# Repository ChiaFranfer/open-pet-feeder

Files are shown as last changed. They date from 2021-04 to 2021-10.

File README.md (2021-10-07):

# Open Pet Feeder

Trabajo final de estudios para finalizar mi titulación 'Ingeniería en Sistemas de Telecomunicación', en la Universidad Politécnica de Cartagena. 
* Nombre del trabajo: `Diseño y automatización de un sistema de alimentación OpenSource para animales a través de la tecnología LoRa`
* Promoción: `2020-2021`

## Objetivos
- Diseñar un sistema de alimentación para animales con tecnologías Open Source.
- Realizar simulaciones para el enlace radio entre el refugio de animales y el emplazamiento de nuestro gateway.
- Construir el prototipo y probarlo en entorno controlado y, posteriormente, en entorno definitivo (refugio).

## Logros conseguidos

- El dispositivo del refugio es apto para trabajar en zonas sin conexión a internet y sin red eléctrica.
- Control remoto de un dispositivo apto para alimentar y abrevar animales.
- Enlace radio LoRa directo (sin repetidores) a varios kilómetros entre gateway y dispositivo.
- Página web de control y envío de comandos al dispositivo.
- Kit gateway + dispositivo, por debajo de 100 euros.

## Tecnologías utilizadas
* Arduino Nano
* Trasnceptor LoRa E32-868T30D
* Raspberry Pi 3
* PCB custom diseñada con EasyEDA

## Imagenes de los dispositivos
### Dispositivo de alimentación y abrevadero


### PCB del dispositivo


## Esquemático del proyecto
### Comedero
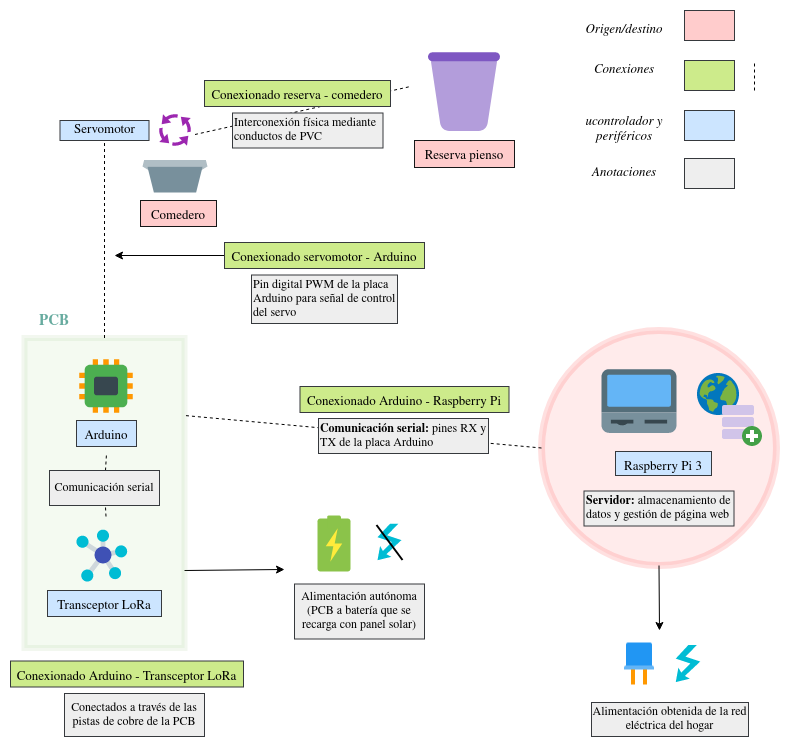
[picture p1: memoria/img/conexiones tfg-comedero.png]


### Bebedero
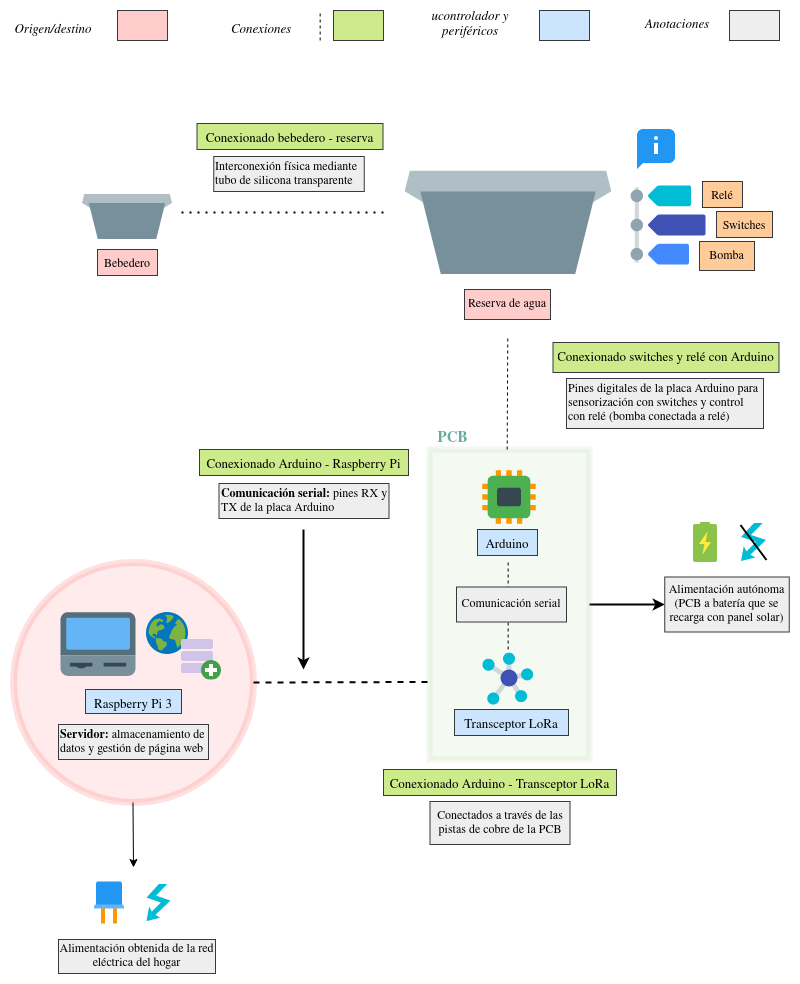
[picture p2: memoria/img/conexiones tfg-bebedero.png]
Diagrama bebedero


### Web


## Documentación
Toda la documentación del proyecto la podemos encontrar en la carpeta: `memoria`. El código utilizado en los diferentes dispositvos se encuentra en la carpeta `software`, y los esquemáticos de la PCB están en la carpeta: `hardware`.

El documento definitivo que se publicará por la universidad está en: `memoria/memoria_definitivo.pdf`

## Autor

- [@ChiaFranfer](https://www.github.com/chiafranfer)

## Licencia
Todo el código del repositorio está bajo la licencia MIT. Los documentos LaTeX y sus PDFs correspondientes pertenecen al autor del proyecto. El trabajo definitivo será publicado por la institución: Universidad Politécnica de Cartagena.

[MIT](https://choosealicense.com/licenses/mit/)

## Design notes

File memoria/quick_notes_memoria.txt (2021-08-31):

## Anotaciones

- Se recomienda ver el tipo de licencia que tiene cada proyecto, ya que aunque sean Open Source, 
presentan por norma general licencias que, como mínimo, exigen que se mencione al creador debidamente.

## Refs a anexos
\hyperref[anexo I: ficha tecnica]{Anexo I}
\hyperref[anexo II: codigo]{Anexo II}
\hyperref[anexo III: presupuesto]{Anexo III}

## Comillas

`` hdajhdahkd ''

## Hackeo de imagenes: 5 imagenes
	\begin{figure}
		\begin{center}
			\begin{tabular}{cc}
				\includegraphics[width=50mm]{img/Fotos comedero/pieza1_comedero.jpg} &   \includegraphics[width=50mm]{img/Fotos comedero/pieza2_comedero.jpg} \\
				(a) Pieza 1 PVC & (b) Pieza 2 PVC \\[6pt]
				\includegraphics[width=50mm]{img/Fotos comedero/pieza3_comedero.jpg} &   \includegraphics[width=50mm]{img/Fotos comedero/pieza4_comedero.jpg} \\
				(c) Pieza 3 PVC & (d) Pieza 4 PVC \\[6pt]
				\multicolumn{2}{c}{\includegraphics[width=50mm]{img/Fotos comedero/pieza5_comedero.jpg} }\\
				\multicolumn{2}{c}{(e) Pieza 5 PVC}
			\end{tabular}
			\caption{Zoom de las piezas que conforman el sistema de conexionado entre reserva y comedero.}
			\label{Prototipo: piezas PVC reserva-comedero}
		\end{center}
	\end{figure}

## Hackeo de imagenes: 2 imagenes

	\begin{figure}
		\begin{center}
			\begin{tabular}{cc}
				\includegraphics[width=50mm]{img/Fotos comedero/pieza1_comedero.jpg} &   \includegraphics[width=50mm]{img/Fotos comedero/pieza2_comedero.jpg} \\
				(a) Pieza 1 PVC & (b) Pieza 2 PVC \\[6pt]
			\end{tabular}
			\caption{Zoom de las piezas que conforman el sistema de conexionado entre reserva y comedero.}
			\label{Prototipo: piezas PVC reserva-comedero}
		\end{center}
	\end{figure}

## Revisar

	Integridad mediante prototipo exterior. Cambiar un poco maybe lo que es el título.

	\item \textbf{Integridad mediante prototipo exterior}. Se entiende por \textit{Integridad mediante prototipo exterior} todos aquellos 
	elementos que usemos para dar forma al proyecto, evitando el uso de elementos demasiado temporales como pueden ser una protoboard o en 
	general, componentes no definitivos (estos sólo se usarán en pruebas, no en producción). Con esta  idea, se buscarán elementos que 
	permitan constituir un primer prototipo usable, sin invertir excesivo dinero, que elimine componentes temporales no funcionales para usar 
	en la ubicación real; es por ello, que se cuenta con la inversión en reservas, conexionado de reserva a comedero/bebedero, diseño de una PCB, etc.

	Apartado 4.2.1.2. Bebedero
	Apartado 4.2.1.1. Comedero

	Explicación de las pruebas de campo -- HECHO
	Explicación de las pruebas de interior

	Explicación del por qué de elegir los E32 (características técnicas)

	Bloque "Software Arduino" -- HECHO

	Fotos Arduino nano

	Foto conglomerado alimentación soldado -- HECHO

## Bib Arduino memory

bib: arduino memory foundations
bib: seeedstudio arduino memory
bib: electronicsHub arduino memory

## Bib bootloader

bib: Arduino cc  bootloader
bib: baldEngineer arduino bootloader

## Bib para leer SPI, uart

https://www.arduino.cc/en/reference/SPI
https://www.circuitbasics.com/basics-of-the-spi-communication-protocol
https://www.circuitbasics.com/basics-uart-communication/

## Insertar una imagen

	\begin{figure}[h]
		\begin{center}
			\includegraphics[width=0.6\textwidth]{img/LPWAN_comp.png}
			\caption{Comparativa entre LPWAN, en términos de alcance y ancho de banda, con respecto a otras comunicaciones inalámbricas [\ref{bib: iotforall lpwan options}].}
			\label{LPWANs vs otros}
		\end{center}
	\end{figure}

## Copiar código a memoria

\begin{lstlisting}[language=C]

\end{lstlisting}

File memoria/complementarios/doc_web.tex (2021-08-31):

\documentclass[12pt]{article}
\usepackage[spanish, english, es-tabla]{babel}
\usepackage[utf8]{inputenc}
\usepackage{amsmath,amssymb}
\usepackage{graphicx}
\usepackage{gensymb}
\usepackage{outlines}
\usepackage[export]{adjustbox}
\usepackage{adjustbox}
\usepackage{multicol}
\usepackage{lipsum}
\parskip 1ex

\usepackage{eurosym}

% add code
\usepackage{listings}

\usepackage{array}

% text font 

\usepackage{courier}

%\usepackage{fontspec}

\usepackage[dvipsnames]{xcolor}

\usepackage{hyperref}
\usepackage{subcaption}
\usepackage[left = 2cm, right = 2cm, bottom = 2cm, top = 3cm]{geometry}

\hypersetup{
	colorlinks=true,
	linkcolor=black,
	%filecolor=magenta,      
	urlcolor=cyan,
}

\hypersetup{
	pdftitle= {Diseño y automatización de un sistema de alimentación OpenSource para animales a través de la tecnología LoRa},
	pdfauthor = {Lucía Francoso Fernández},
	pdfsubject = {Electrónica y comunicaciones móviles},
	pdfkeywords = {Arduino, LoRa, automatización, LoRaWAN, punto a punto, OpenSource}
}

% define color for C code (Anexos)

\definecolor{codegreen}{rgb}{0,0.6,0}
\definecolor{codegray}{rgb}{0.5,0.5,0.5}
\definecolor{codepurple}{rgb}{0.58,0,0.82}
\definecolor{backcolour}{rgb}{0.95,0.95,0.92}

\lstdefinestyle{mystyle}{
	backgroundcolor=\color{backcolour},   
	commentstyle=\color{codegreen},
	keywordstyle=\color{magenta},
	numberstyle=\tiny\color{codegray},
	stringstyle=\color{codepurple},
	basicstyle=\ttfamily\footnotesize,
	breakatwhitespace=false,         
	breaklines=true,                 
	captionpos=b,                    
	keepspaces=true,                 
	numbers=left,                    
	numbersep=5pt,                  
	showspaces=false,                
	showstringspaces=false,
	showtabs=false,                  
	tabsize=2
}

\lstset{style=mystyle}

% https://tex.stackexchange.com/questions/60209/how-to-add-an-extra-level-of-sections-with-headings-below-subsubsection
\newcommand{\subsubsubsection}[1]{\paragraph{#1}\mbox{}\\}
\setcounter{secnumdepth}{4}
\setcounter{tocdepth}{4}

\begin{document}
	\selectlanguage{spanish}
	
	%\thispagestyle{empty}

	%\pagebreak
	
	\thispagestyle{empty}
	
	\newgeometry{left=0.01cm,bottom=0.01cm, top=0.01cm}
	
	%width=0.3\textwidth,
	
	%\begin{figure}[h!]
	%	\includegraphics[height=\textheight,left]{img/banda_etsit_90.png}
	
	%	\end{figure}
	
	\begin{minipage}{0.2\textwidth}
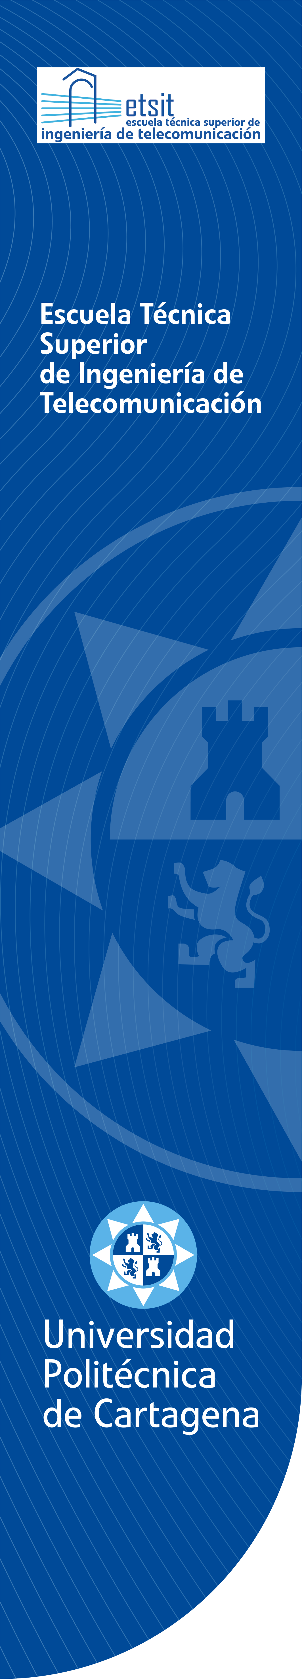
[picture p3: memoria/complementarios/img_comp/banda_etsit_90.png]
		
	\end{minipage}
	\centerline{\begin{minipage}[t][7cm][b]{0.5\textwidth}
			%	\textbf{UNIVERSIDAD POLITÉCNICA DE} \\
			
			%	\textbf{CARTAGENA}\\
			
			\vspace{2cm}
			
			\title{\textbf{Automatización y control de bebederos automáticos para especies animales usando LoRa: }\\
				
			\vspace{1cm}
			
			\textit{Documentación de la página web} 
			}
			
			\maketitle
			
			\vspace{1cm}
				
			\hspace{1.5cm} \textbf{TRABAJO FIN DE GRADO} \\
			
			\vspace{0.5cm}
			
			\hspace{1.3cm} Grado en Ingeniería en Sistemas  de\\
			
			\vspace{0.01cm}
			
			\hspace{2.7cm} Telecomunicaciones \\
			
			\vspace{1cm}
			
			\textbf{Autora:}\author{ Lucía Francoso Fernández}\\
			
			\textbf{Tutor:} Juan Pascual García
	\end{minipage}}

	\restoregeometry
	
	\pagebreak

	\tableofcontents
	
	\pagebreak
	
	\listoffigures
	\addcontentsline{toc}{section}{Índice de figuras}
	
	\pagebreak
	
	\listoftables
	\addcontentsline{toc}{section}{Índice de tablas}
	
	\pagebreak
	
	\section{Introducción}
	
	\noindent En este documento se recoge una pequeña documentación sobre la página web \textit{Open Pet Feeder}, una web creada bajo el marco del Trabajo Fin de Grado especificado en el título del presente, \textit{Automatización y control de bebederos automáticos para especies animales usando LoRa}. Es una parte fundamental para la consecución de ciertos objetivos del proyecto, entre ellos, la monitorización de la estación que se situará en el refugio de Patitas Unidas Los Alcázares, desde cualquier dispositivo y desde cualquier sitio (dentro o fuera de la red local de la estación donde se sitúa el servidor que almacena la web).\\
	
	\noindent Comprende explicaciones sobre el funcionamiento de la misma, así como explicaciones sobre la creación de la web. Para una introducción a la página web más visual, se incluyen capturas bajo diferentes situaciones.\\
	
	\section{Apariencia de la web}
	
	\begin{figure}[h!]
		\begin{center}
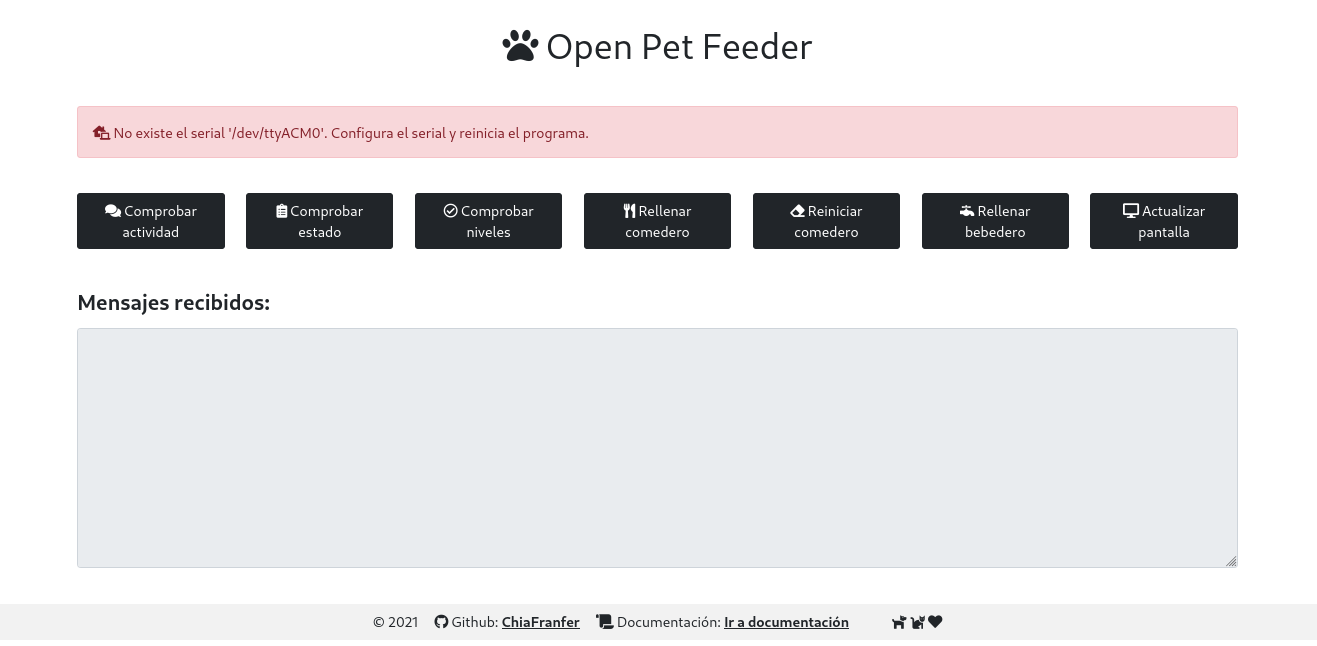
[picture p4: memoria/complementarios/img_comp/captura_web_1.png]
			
			\caption{Captura de la web \textit{Open Pet Feeder}, donde se muestra el mensaje de error al no detectar la conexión serial con el arduino.}
			\label{captura web 1}
		\end{center}
	\end{figure}

	\pagebreak
	
	\begin{figure}[h!]
		\begin{center}
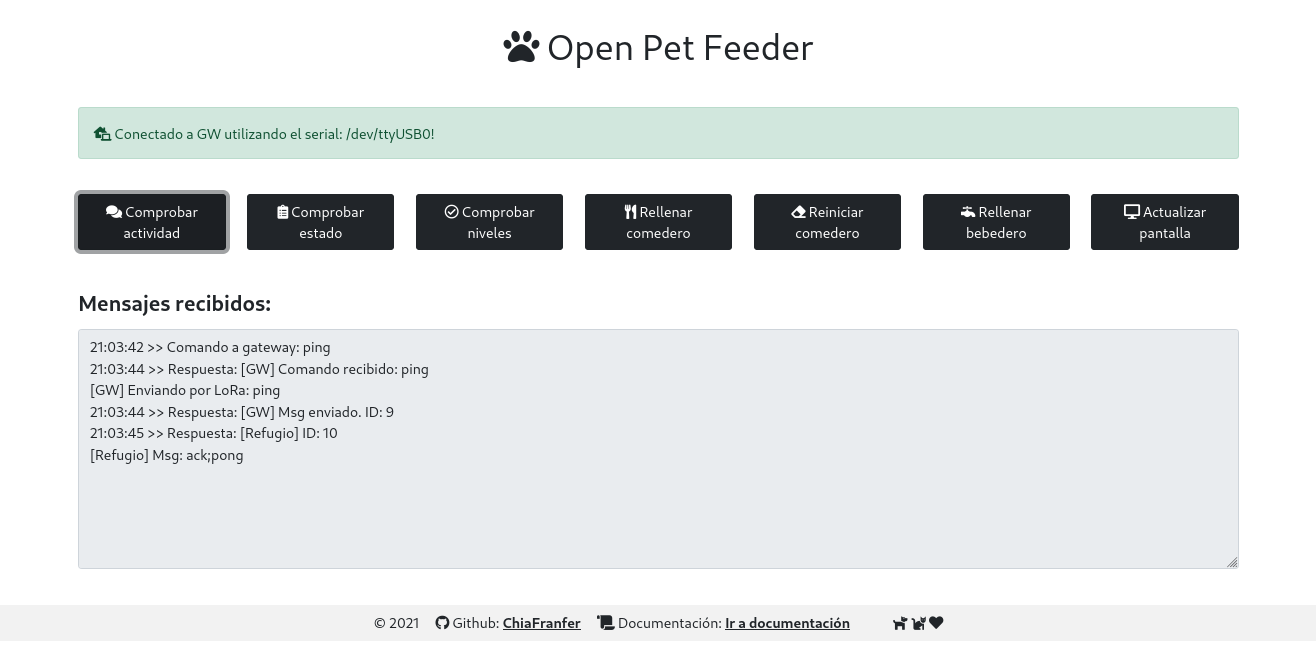
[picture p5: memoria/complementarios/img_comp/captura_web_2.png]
			
			\caption{Captura de la web \textit{Open Pet Feeder}, donde se muestra en la consola la interacción entre estación del campo y estación del refugio a través del comando \textit{ping} (botón \textit{Comprobar actividad}).}
			\label{captura web 2}
		\end{center}
	\end{figure}
	
	\pagebreak
	
	\begin{figure}[h!]
		\begin{center}
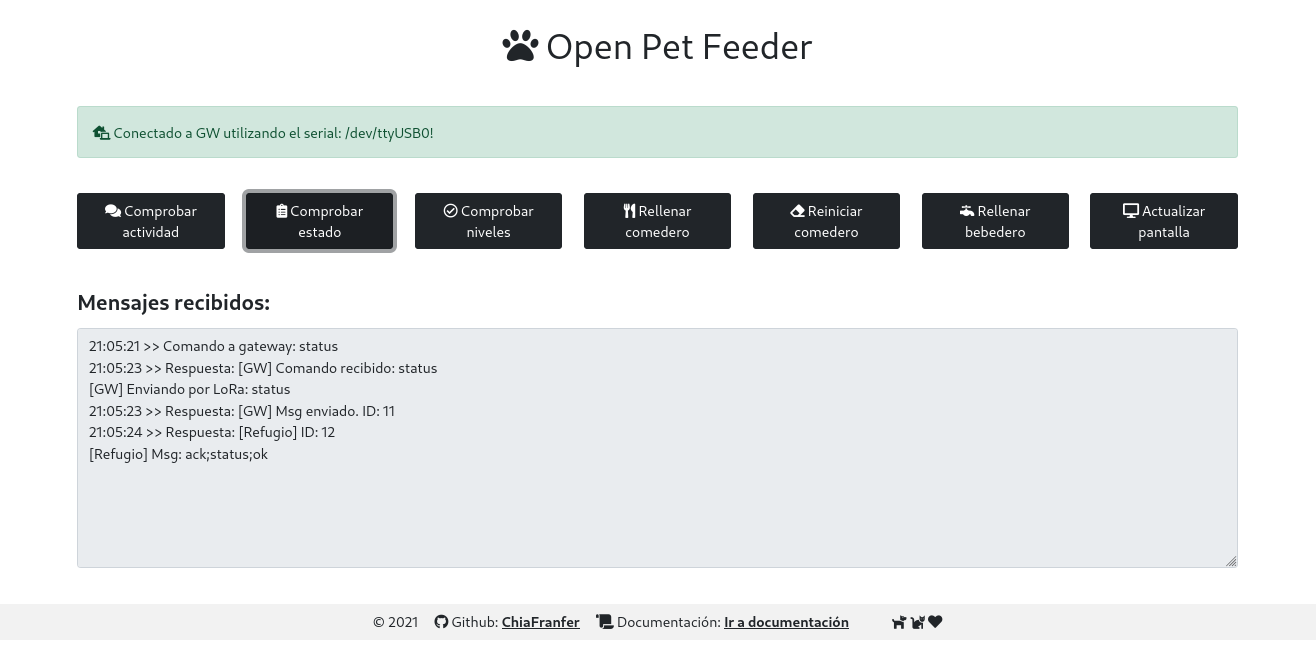
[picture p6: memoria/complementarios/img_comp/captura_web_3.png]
			
			\caption{Captura de la web \textit{Open Pet Feeder}, donde se muestra en la consola la interacción entre estación del campo y estación del refugio a través del comando \textit{status} (botón \textit{Comprobar estado}).}
			\label{captura web 3}
		\end{center}
	\end{figure}

	\pagebreak
	
	\begin{figure}[h!]
		\begin{center}
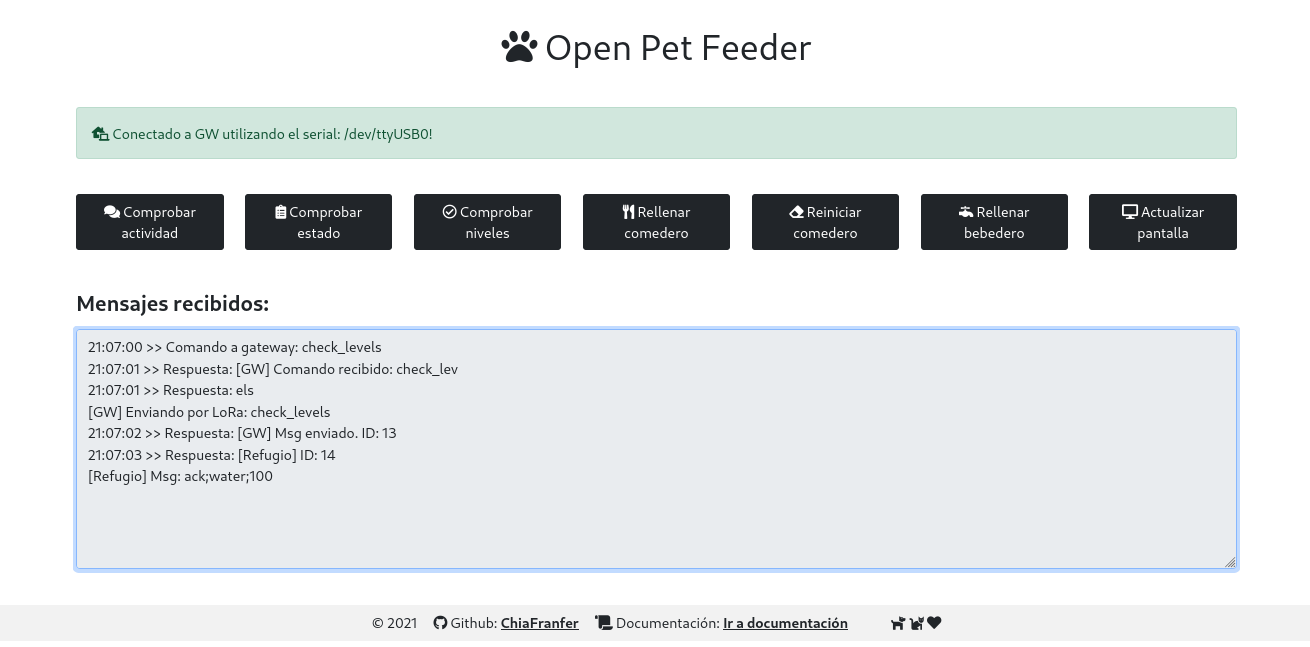
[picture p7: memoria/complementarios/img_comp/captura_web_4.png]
			
			\caption{Captura de la web \textit{Open Pet Feeder}, donde se muestra en la consola la interacción entre estación del campo y estación del refugio a través del comando \textit{check\_levels} (botón \textit{Comprobar niveles}).}
			\label{captura web 4}
		\end{center}
	\end{figure}

	\pagebreak
	
	\begin{figure}[h!]
		\begin{center}
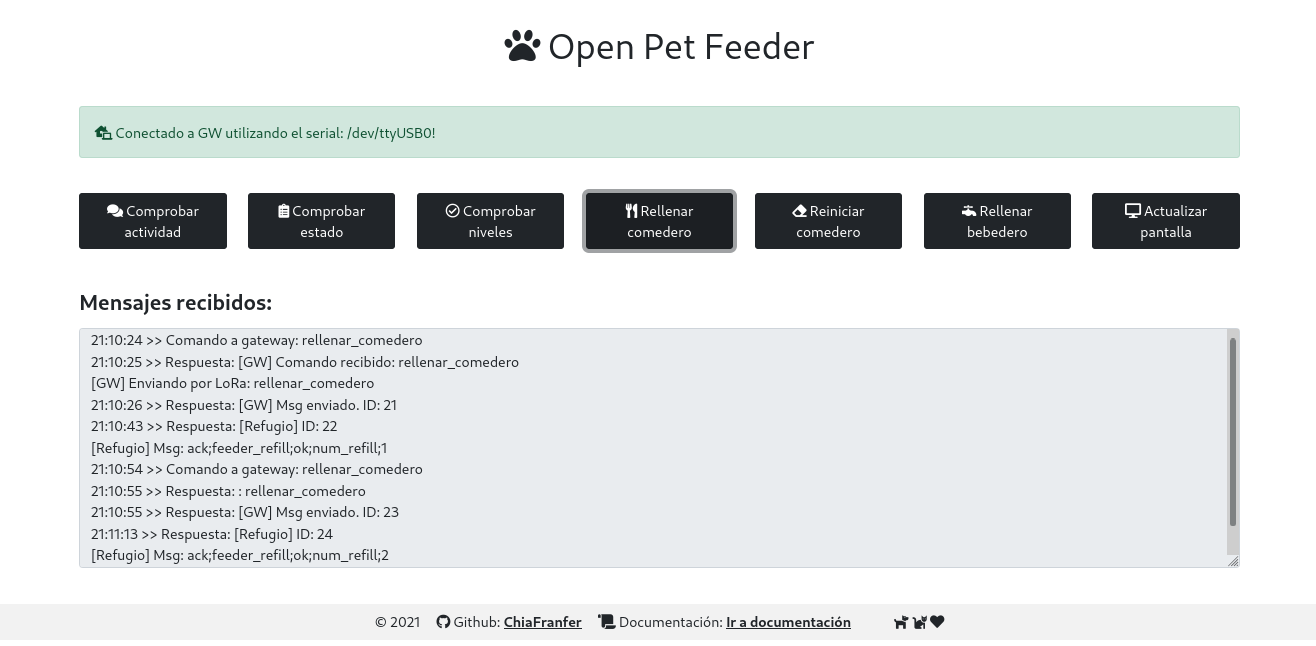
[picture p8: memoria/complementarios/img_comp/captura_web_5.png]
			
			\caption{Captura de la web \textit{Open Pet Feeder}, donde se muestra en la consola la interacción entre estación del campo y estación del refugio a través del comando \textit{rellenar\_comedero} (botón \textit{Rellenar comedero}).}
			\label{captura web 5}
		\end{center}
	\end{figure}

	\pagebreak
	
	\begin{figure}[h!]
		\begin{center}
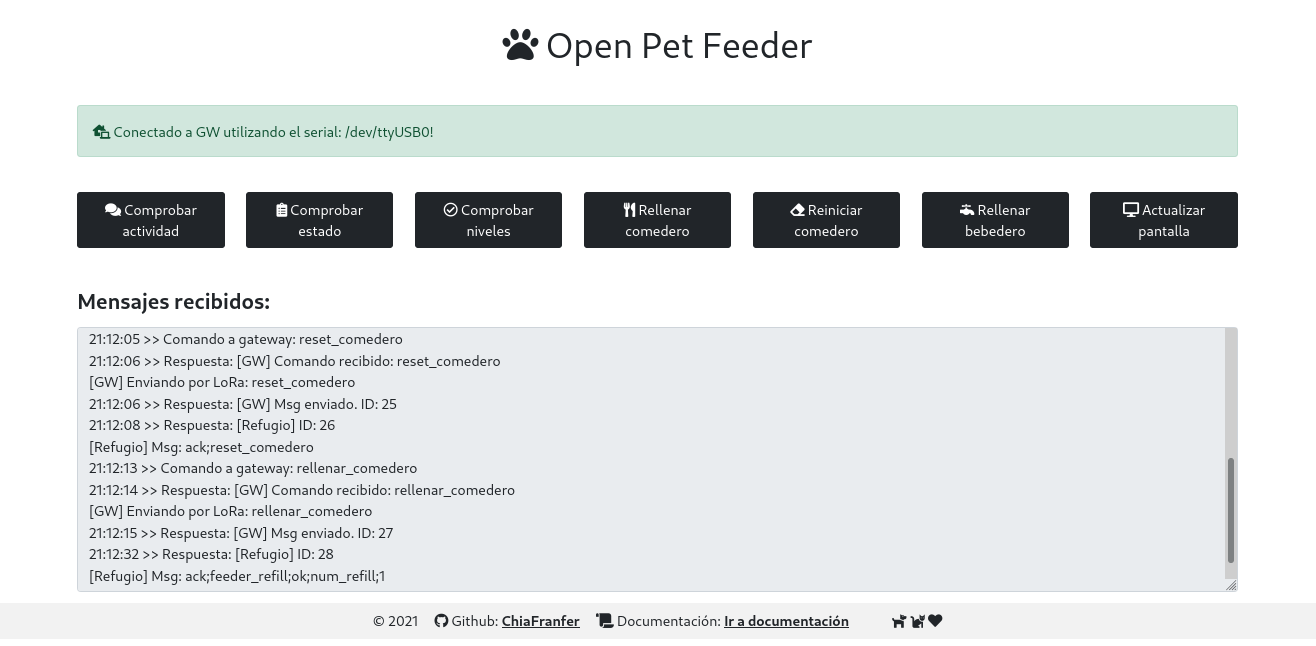
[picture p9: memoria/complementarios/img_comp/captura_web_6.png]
			
			\caption{Captura de la web \textit{Open Pet Feeder}, donde se muestra en la consola la interacción entre estación del campo y estación del refugio a través del comando \textit{reset\_comedero} (botón \textit{Reiniciar comedero}).}
			\label{captura web 6}
		\end{center}
	\end{figure}

	\pagebreak
	
	\begin{figure}[h!]
		\begin{center}
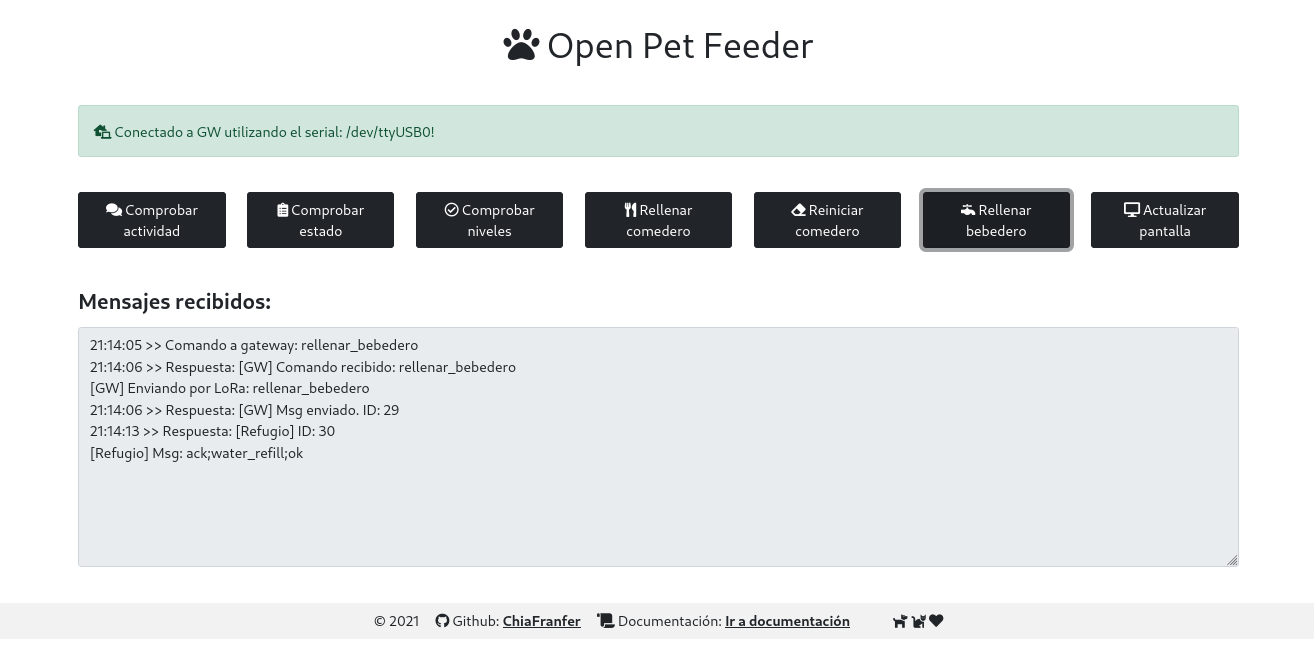
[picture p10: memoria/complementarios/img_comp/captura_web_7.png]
			
			\caption{Captura de la web \textit{Open Pet Feeder}, donde se muestra en la consola la interacción entre estación del campo y estación del refugio a través del comando \textit{rellenar\_bebedero} (botón \textit{Rellenar bebedero}).}
			\label{captura web 7}
		\end{center}
	\end{figure}
	
	\noindent El botón \textit{Actualizar pantalla} (comando asociado \textit{update\_oled}) no realiza la función que describe su nombre, ya que no se implementó a nivel arduino por ocupar más espacio del disponible en el arduino nano (la librería \textit{OLED} ocupa bastante espacio). Si se envía este comando, la estación del refugio devuelve un string con ``\textit{to do}'', indicando que hay que implementarlo.\\
	
	\pagebreak
	
	\section*{Anexo}
	\addcontentsline{toc}{section}{Anexo}
	\label{anexo: codigo}
	
	\noindent En este anexo, se incluye el código empleado para crear la web. \\
	
	\noindent \textit{\textbf{Aplicación web}}: \textit{app.py}\\
	
	\begin{lstlisting}[language=python]
import engineio
from flask import Flask, render_template
from flask_socketio import SocketIO
from flask_serial import Serial
from datetime import datetime

import json
import socketio
import os

app = Flask(__name__)

## Configuration Serial GW
serial_port = '/dev/ttyUSB0'                    # Modificar aqui el serial del Arduino, lo dice el IDE
app.config['SERIAL_PORT'] = serial_port
app.config['SERIAL_TIMEOUT'] = 0.1
app.config['SERIAL_BAUDRATE'] = 115200
app.config['SERIAL_BYTESIZE'] = 8
app.config['SERIAL_PARITY'] = 'N'
app.config['SERIAL_STOPBITS'] = 1

socketio = SocketIO(app, async_mode="gevent", ping_timeout=5, logger=False, engineio_logger=False)
ser = Serial(app)

#
#   Enpoints
#

# Endpoint home page
@app.route("/")
def index():
# Comprobamos que el serial existe
if os.path.exists(serial_port):
serial_exists = True
else:
serial_exists = False

return render_template("index.html", serial_port=serial_port, serial_exists=serial_exists)

# Endpoint documentation page
@app.route("/doc")
def doc():
return render_template("doc.html")

#
#   SocketIO
#

# Handler SocketIO [messages of web]
@socketio.on('send')
def handle_send(json_str):
data = json.loads(json_str)["message"]
print("Boton pulsado: {}".format(data))

# Enviamos por serial
try:
ser.on_send(data)
except Exception as ex:
print("Error on serial: {}".format(ex))

# Enviamos en el socket 'receive_message' [hacer en recepcion serial]
now = datetime.now()
msg = "{} >> Comando a gateway: {}".format(now.strftime("%H:%M:%S"), data)
socketio.emit("receive_message", data={"message":str(msg)})

#
#   Flask-Serial
#

# Handler incoming serial messages
@ser.on_message()
def handle_message(msg):
try:
print("receive message: {}".format(msg))
now = datetime.now()
msg = "{} >> Respuesta: {}".format(now.strftime("%H:%M:%S"), msg.decode("utf-8").strip('\n'))
print("Send socket msg: {}".format(msg))
socketio.emit("receive_message", data={"message":str(msg)})
except Exception as ex:
print(ex)

# Log thread serial
@ser.on_log()
def handle_logging(level, info):
print(level, info)

if __name__ == '__main__':
socketio.run(app, debug=False, log_output=True)
	\end{lstlisting}

	\noindent \textit{\textbf{Página principal de la web}}: \textit{index.html}\\
	
	\begin{lstlisting}[language=html]
<!doctype html>
<html lang="es">
<head>
<!-- Required meta tags -->
<meta charset="utf-8">
<meta name="viewport" content="width=device-width, initial-scale=1">
<link rel="icon" type="image/png" href="static/favicon.ico">

<!-- Bootstrap CSS -->
<link href="https://cdn.jsdelivr.net/npm/bootstrap@5.0.2/dist/css/bootstrap.min.css" rel="stylesheet" integrity="sha384-EVSTQN3/azprG1Anm3QDgpJLIm9Nao0Yz1ztcQTwFspd3yD65VohhpuuCOmLASjC" crossorigin="anonymous">
<link rel="stylesheet" href="https://cdnjs.cloudflare.com/ajax/libs/font-awesome/5.15.3/css/all.min.css" integrity="sha512-iBBXm8fW90+nuLcSKlbmrPcLa0OT92xO1BIsZ+ywDWZCvqsWgccV3gFoRBv0z+8dLJgyAHIhR35VZc2oM/gI1w==" crossorigin="anonymous" referrerpolicy="no-referrer" />
<script src="https://cdn.socket.io/3.1.3/socket.io.min.js" integrity="sha384-cPwlPLvBTa3sKAgddT6krw0cJat7egBga3DJepJyrLl4Q9/5WLra3rrnMcyTyOnh" crossorigin="anonymous"></script>
<script src="https://code.jquery.com/jquery-3.6.0.min.js" integrity="sha256-/xUj+3OJU5yExlq6GSYGSHk7tPXikynS7ogEvDej/m4=" crossorigin="anonymous"></script>

<title>Open Pet Feeder</title>
</head>
<body>
<h1 style="text-align: center; margin-top: 2%;"><a href="/" style="text-decoration: none; color: inherit;"><i class="fas fa-paw"></i> Open Pet Feeder</a></h1>

<div class="container" style="margin-top: 3%;">
{% if serial_exists == True %}
	<div class="alert alert-success" role="alert" style="margin-bottom: 3%;">
	<i class="fas fa-laptop-house"></i> Conectado a GW utilizando el serial: {{serial_port}}!
	</div>
	{% else %}
		<div class="alert alert-danger" role="alert" style="margin-bottom: 3%;">
		<i class="fas fa-laptop-house"></i> No existe el serial '{{serial_port}}'. Configura el serial y reinicia el programa.
		</div>
		{% endif %}
			
			<div class="row" style="text-align: center;">
			<div class="col">
			<button type="button" class="btn btn-dark mt-1" id="send_ping" value="ping"><i class="fas fa-comments"></i>  Comprobar actividad</button>
			</div>
			<div class="col">
			<button type="button" class="btn btn-dark mt-1" id="send_status" value="status"><i class="fas fa-clipboard-list"></i>  Comprobar estado</button>
			</div>
			<div class="col">
			<button type="button" class="btn btn-dark mt-1" id="send_check_levels" value="check_levels"> <i class="far fa-check-circle"></i>  Comprobar niveles</button>
			</div>
			<div class="col">
			<button type="button" class="btn btn-dark mt-1" id="send_comedero" value="rellenar_comedero"><i class="fas fa-utensils"></i> Rellenar comedero</button>
			</div>
			<div class="col">
			<button type="button" class="btn btn-dark mt-1" id="send_reset_comedero" value="reset_comedero"><i class="fas fa-eraser"></i> Reiniciar comedero</button>
			</div>
			<div class="col">
			<button type="button" class="btn btn-dark mt-1" id="send_bebedero" value="rellenar_bebedero"><i class="fas fa-faucet"></i> Rellenar bebedero</button>
			</div>
			
			<div class="col">
			<button type="button" class="btn btn-dark mt-1" id="send_oled" value="update_oled"><i class="fas fa-desktop"></i> Actualizar pantalla</button>
			</div>
			</div>
			</div>
			
			<div class="container" style="margin-top: 3%;">
			<div class="console">
			<label class="form-label" for="receive"> <h4> <b>Mensajes recibidos:</b> </h4>  </label>
			<textarea readonly class="form-control" name="receive" id="receive" rows="8" style="width: 100%; height: auto;"></textarea>
			</div>
			</div>
			
			<!-- Footer -->
			<div class="footer fixed-bottom mt-4 py-4">
			<div class="text-center p-2" style="background-color: rgba(0, 0, 0, 0.05); margin-bottom: -1%;">
			C  2021  <i class="fab fa-github" style="margin-left: 1%;"></i> Github:
			<a class="text-reset fw-bold" href="https://github.com/ChiaFranfer">ChiaFranfer</a> 
			<i class="fas fa-scroll" style="margin-left: 1%;"></i> Documentacion: <a class="text-reset fw-bold" href="{{url_for('doc')}}"> Ir a documentacion</a>
			<i class="fas fa-dog" style="margin-left: 3%;"></i> <i class="fas fa-cat"></i> <i class="fas fa-heart"></i>
			</div>
			</div>
			
			<script src="https://cdn.jsdelivr.net/npm/bootstrap@5.0.2/dist/js/bootstrap.bundle.min.js" integrity="sha384-MrcW6ZMFYlzcLA8Nl+NtUVF0sA7MsXsP1UyJoMp4YLEuNSfAP+JcXn/tWtIaxVXM" crossorigin="anonymous"></script>
			<script type="text/javascript" charset="utf-8">
			$(document).ready(function() {
				var socket = io.connect('http://' + document.domain + ':' + location.port);
				
				$('#send_status').on('click', function() {
					var message = $(this)[0].value;
					console.log('Enviando: ' + message);
					var data = '{' + '"message": "' + message + '"}';
					socket.emit('send', data=data);
				});
				
				$('#send_ping').on('click', function() {
					var message = $(this)[0].value;
					console.log('Enviando: ' + message);
					var data = '{' + '"message": "' + message + '"}';
					socket.emit('send', data=data);
				});
				
				$('#send_reset_comedero').on('click', function() {
					var message = $(this)[0].value;
					console.log('Enviando: ' + message);
					var data = '{' + '"message": "' + message + '"}';
					socket.emit('send', data=data);
				});
				
				$('#send_comedero').on('click', function() {
					var message = $(this)[0].value;
					console.log('Enviando: ' + message);
					var data = '{' + '"message": "' + message + '"}';
					socket.emit('send', data=data);
				});
				
				$('#send_bebedero').on('click', function() {
					var message = $(this)[0].value;
					console.log('Enviando: ' + message);
					var data = '{' + '"message": "' + message + '"}';
					socket.emit('send', data=data);
				});
				
				$('#send_check_levels').on('click', function() {
					var message = $(this)[0].value;
					console.log('Enviando: ' + message);
					var data = '{' + '"message": "' + message + '"}';
					socket.emit('send', data=data);
				});
				
				$('#send_oled').on('click', function() {
					var message = $(this)[0].value;
					console.log('Enviando: ' + message);
					var data = '{' + '"message": "' + message + '"}';
					socket.emit('send', data=data);
				});
				
				socket.on('receive_message', function(data){
					console.log(data);
					var text = data['message'];
					var $textarea = $('#receive');
					$textarea.val($textarea.val() + text + '\n');
					$textarea.scrollTop($textarea[0].scrollHeight);
				})
			});
			
			</script>
			</body>
			</html>
	\end{lstlisting}

\end{document}

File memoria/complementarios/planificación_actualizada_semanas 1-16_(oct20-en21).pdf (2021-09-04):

| 1 | 2 | 3 | 4 | 5 | 6 | 7 | 8 | 9 | 10 | 11 | 12 | 13 | 14 | 15 | 16
Tareas | 12-oct-2020 | 19-oct-2020 | 26-oct-2020 | 2-nov-2020 | 9-nov-2020 | 16-nov-2020 | 23-nov-2020 | 30-nov-2020 | 7-dic-2020 | 14-dic-2020 | 21-dic-2020 | 28-dic-2020 | 4-ene-2021 | 11-ene-2021 | 18-ene-2021 | 25-ene-2021

Análisis y compra de dispositivos
- Kit de arduino
- TTGO LoRa (pruebas)
- Bomba de agua
- Tarjeta SD Raspberry Pi
- Gateway LoRa
- Alimentación
- ¿Otro sensor de nivel de agua?
- ¿Otro servo motor?
- ¿Otro pack TTGO?
- Otros

Estudio de LoRa
- Estudio del protocolo
- Estudio de dispositivos TX/RX
- Conexión con Arduino
- Pruebas y debugging

Estudio de Arduino
- Estudio lenguaje
- Estudio sensores
- Programación
- Pruebas y debugging

Creación base de datos Rasp.
- Creación BBDD
- Conexión Raspberry Pi con TTGO
- Pruebas y debugging

Visualización datos
- Ver datos en local
- Programación página web
- Pruebas y debugging

Integración componentes
- TTGO, Arduino, sensores, motores
- Pruebas. Documentar resultados
- Estudio consumo energía
- Determinar sist. alimentación
- Esbozo prototipo definitivo

Integración con fuente alim.
- Pruebas con fuente alim.
- Prototipo definitivo
- Debugging fallos encontrados

Pruebas en entorno controlado
- Pruebas
- Debugging fallos encontrados

Pruebas en entorno real
- Pruebas
- Debugging fallos encontrados Mejoras en prototipo final
- Mayor eficiencia energética
- Mejor aspecto externo
- Mejor comunicación TX/RX
- Otros

Redacción memoria final

Redacción memoria final
Presentación TFG
Presentación TFG

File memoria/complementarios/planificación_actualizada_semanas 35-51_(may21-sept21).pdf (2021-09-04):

| 35 | 36 | 37 | 38 | 39 | 40 | 41 | 42 | 43 | 44 | 45 | 46 | 47 | 48 | 49 | 50 | 51
Tareas | 7-jun-2021 | 14-jun-2021 | 21-jun-2021 | 28-jun-2020 | 5-jul-2021 | 12-jul-2021 | 19-jul-2021 | 26-jul-2021 | 2-ago-2021 | 9-ago-2021 | 16-ago-2021 | 23-ago-2021 | 30-ago-2021 | 6-sep.-2021 | 13-sep.-2021 | 20-sep.-2021 | 27-sep.-2021

Análisis y compra de dispositivos
- Kit de arduino
- TTGO LoRa (pruebas)
- Bomba de agua
- Tarjeta SD Raspberry Pi
- Gateway LoRa
- Alimentación
- ¿Otro sensor de nivel de agua?
- ¿Otro servo motor?
- ¿Otro pack TTGO?
- Otros

Estudio de LoRa
- Estudio del protocolo
- Estudio de dispositivos TX/RX
- Conexión con Arduino
- Pruebas y debugging

Estudio de Arduino
- Estudio lenguaje
- Estudio sensores
- Programación
- Pruebas y debugging

Creación base de datos Rasp.
- Creación BBDD
- Conexión Raspberry Pi con TTGO
- Pruebas y debugging

Visualización datos
- Ver datos en local
- Programación página web
- Pruebas y debugging

Integración componentes
- TTGO, Arduino, sensores, motores
- Pruebas. Documentar resultados
- Estudio consumo energía
- Determinar sist. alimentación
- Esbozo prototipo definitivo

Integración con fuente alim.
- Pruebas con fuente alim.
- Prototipo definitivo
- Debugging fallos encontrados

Pruebas en entorno controlado
- Pruebas
- Debugging fallos encontrados

Pruebas en entorno real
- Pruebas
- Debugging fallos encontrados

Mejoras en prototipo final
- Mayor eficiencia energética
- Mejor aspecto externo
- Mejor comunicación TX/RX
- Otros

Redacción memoria final

Redacción memoria final

Presentación TFG

Presentación TFG

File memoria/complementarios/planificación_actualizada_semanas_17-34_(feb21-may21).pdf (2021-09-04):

| 17 | 18 | 19 | 20 | 21 | 22 | 23 | 24 | 25 | 26 | 27 | 28 | 29 | 30 | 31 | 32 | 33 | 34
Tareas | 1-feb-2021 | 8-feb-2021 | 15-feb-2021 | 22-feb-2020 | 1-mar-2021 | 8-mar-2021 | 15-mar-2021 | 22-mar-2021 | 29-mar-2021 | 5-abr-2021 | 12-abr-2021 | 19-abr-2021 | 26-abr-2021 | 3-may-2021 | 10-may-2021 | 17-may-2021 | 24-may-2021 | 31-may-2021

Análisis y compra de dispositivos
- Kit de arduino
- TTGO LoRa (pruebas)
- Bomba de agua
- Tarjeta SD Raspberry Pi
- Gateway LoRa
- Alimentación
- ¿Otro sensor de nivel de agua?
- ¿Otro servo motor?
- ¿Otro pack TTGO?
- Otros

Estudio de LoRa
- Estudio del protocolo
- Estudio de dispositivos TX/RX
- Conexión con Arduino
- Pruebas y debugging

Estudio de Arduino
- Estudio lenguaje
- Estudio sensores
- Programación
- Pruebas y debugging

Creación base de datos Rasp.
- Creación BBDD
- Conexión Raspberry Pi con TTGO
- Pruebas y debugging

Visualización datos
- Ver datos en local
- Programación página web
- Pruebas y debugging

Integración componentes
- TTGO, Arduino, sensores, motores
- Pruebas. Documentar resultados
- Estudio consumo energía
- Determinar sist. alimentación
- Esbozo prototipo definitivo

Integración con fuente alim.
- Pruebas con fuente alim.
- Prototipo definitivo
- Debugging fallos encontrados

Pruebas en entorno controlado
- Pruebas
- Debugging fallos encontrados

Pruebas en entorno real
- Pruebas
- Debugging fallos encontrados Mejoras en prototipo final
- Mayor eficiencia energética
- Mejor aspecto externo
- Mejor comunicación TX/RX
- Otros

Redacción memoria final
Redacción memoria final
Presentación TFG
Presentación TFG

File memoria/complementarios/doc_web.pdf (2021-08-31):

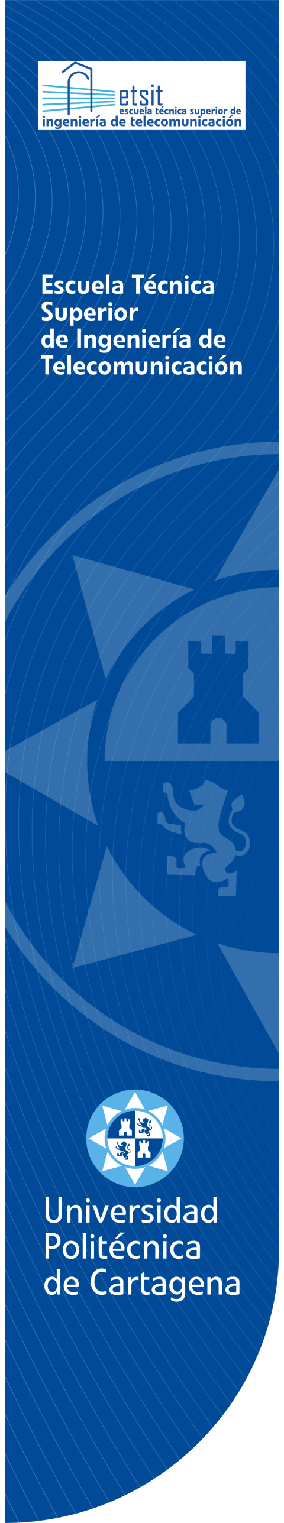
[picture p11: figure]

# Automatización y control de bebederos automáticos para especies animales usando LoRa:

# Documentación de la página web

## 31 de agosto de 2021

## TRABAJO FIN DE GRADO

## Grado en Ingeniería en Sistemas de

## Telecomunicaciones

## Autora: Lucía Francoso Fernández

## Tutor: Juan Pascual García

# Índice

Índice de figuras | 3
Índice de tablas | 4
1 Introducción | 5
2 Apariencia de la web | 5
Anexo | 12

# Índice de figuras

1 | Captura de la web Open Pet Feeder, donde se muestra el mensaje de error al no
detectar la conexión serial con el arduino | | 5
2 | Captura de la web Open Pet Feeder, donde se muestra en la consola la interacción

## entre estación del campo y estación del refugio a través del comando ping (botón

Comprobar actividad) | | 6
3 | Captura de la web Open Pet Feeder, donde se muestra en la consola la interacción

## entre estación del campo y estación del refugio a través del comando status (botón

Comprobar estado) | | 7
4 | Captura de la web Open Pet Feeder, donde se muestra en la consola la interacción

## entre estación del campo y estación del refugio a través del comando check levels

(botón Comprobar niveles) | | 8
5 | Captura de la web Open Pet Feeder, donde se muestra en la consola la interacción en-

## tre estación del campo y estación del refugio a través del comando rellenar comedero

(botón Rellenar comedero) | | 9
6 | Captura de la web Open Pet Feeder, donde se muestra en la consola la interacción

## entre estación del campo y estación del refugio a través del comando reset comedero (botón Reiniciar comedero) | 10

## 7 Captura de la web Open Pet Feeder, donde se muestra en la consola la interacción entre estación del campo y estación del refugio a través del comando rellenar bebedero (botón Rellenar bebedero) | 11

# Índice de tablas

# 1 Introducción

En este documento se recoge una pequeña documentación sobre la página web Open Pet Feeder, una web creada bajo el marco del Trabajo Fin de Grado especificado en el título del presente, Automatización y control de bebederos automáticos para especies animales usando LoRa. Es una parte fundamental para la consecución de ciertos objetivos del proyecto, entre ellos, la monitori-zación de la estación que se situará en el refugio de Patitas Unidas Los Alcázares, desde cualquier dispositivo y desde cualquier sitio (dentro o fuera de la red local de la estación donde se sitúa el servidor que almacena la web).

Comprende explicaciones sobre el funcionamiento de la misma, así como explicaciones sobre la creación de la web. Para una introducción a la página web más visual, se incluyen capturas bajo diferentes situaciones.

# 2 Apariencia de la web


Figura 1: Captura de la web Open Pet Feeder, donde se muestra el mensaje de error al no detectar la conexión serial con el arduino.

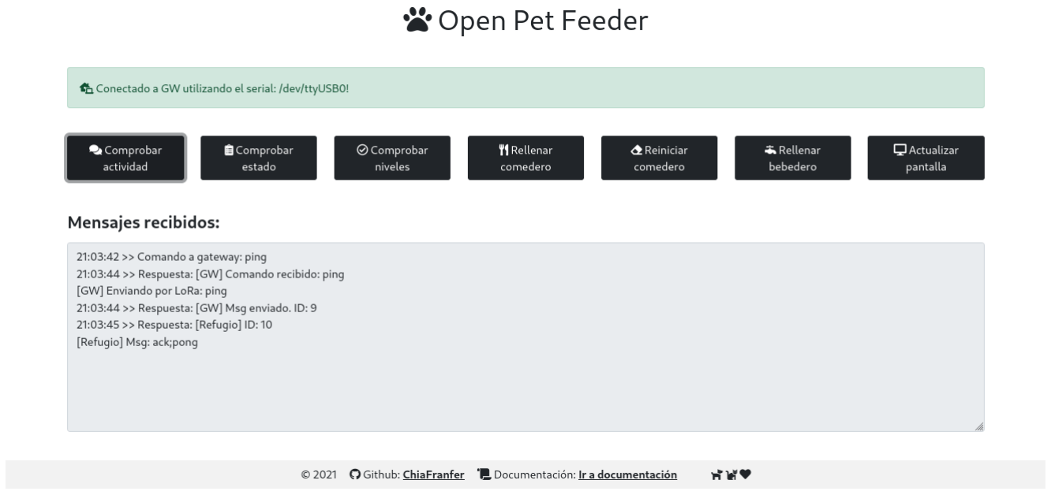
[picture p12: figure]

Figura 2: Captura de la web Open Pet Feeder, donde se muestra en la consola la interacción entre estación del campo y estación del refugio a través del comando ping (botón Comprobar actividad).

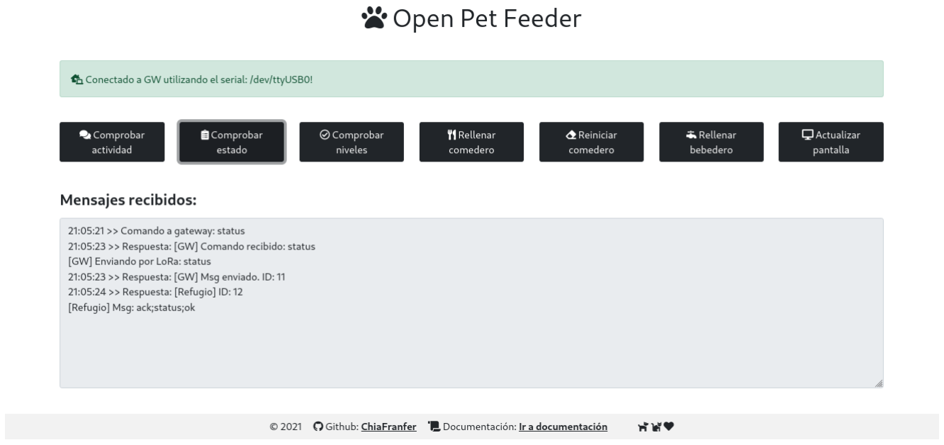
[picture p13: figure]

Figura 3: Captura de la web Open Pet Feeder, donde se muestra en la consola la interacción entre estación del campo y estación del refugio a través del comando status (botón Comprobar estado).


Figura 4: Captura de la web Open Pet Feeder, donde se muestra en la consola la interacción entre estación del campo y estación del refugio a través del comando check levels (botón Comprobar niveles).

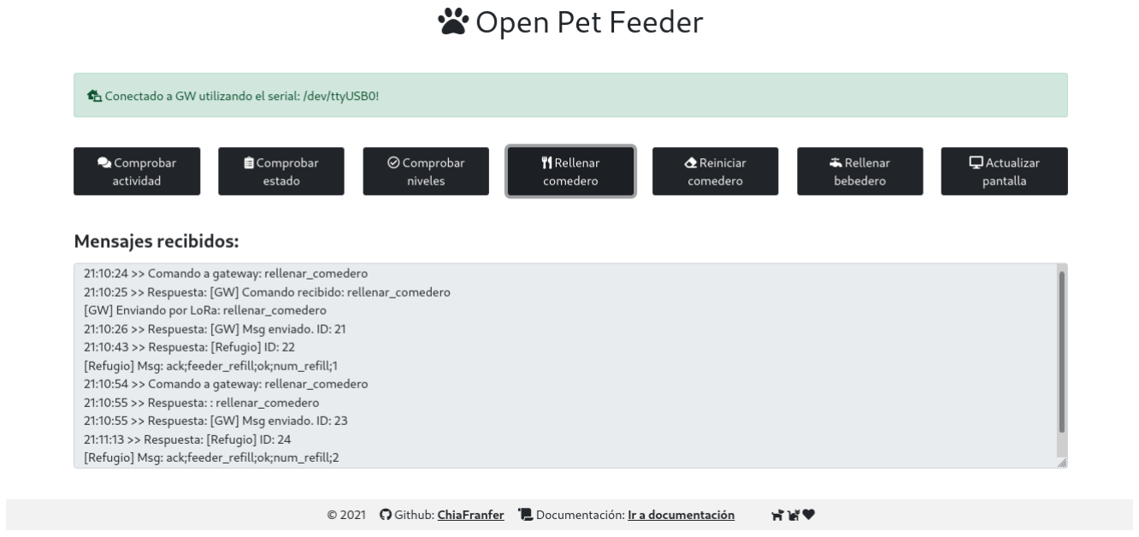
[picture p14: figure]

Figura 5: Captura de la web Open Pet Feeder, donde se muestra en la consola la interacción entre estación del campo y estación del refugio a través del comando rellenar comedero (botón Rellenar comedero).

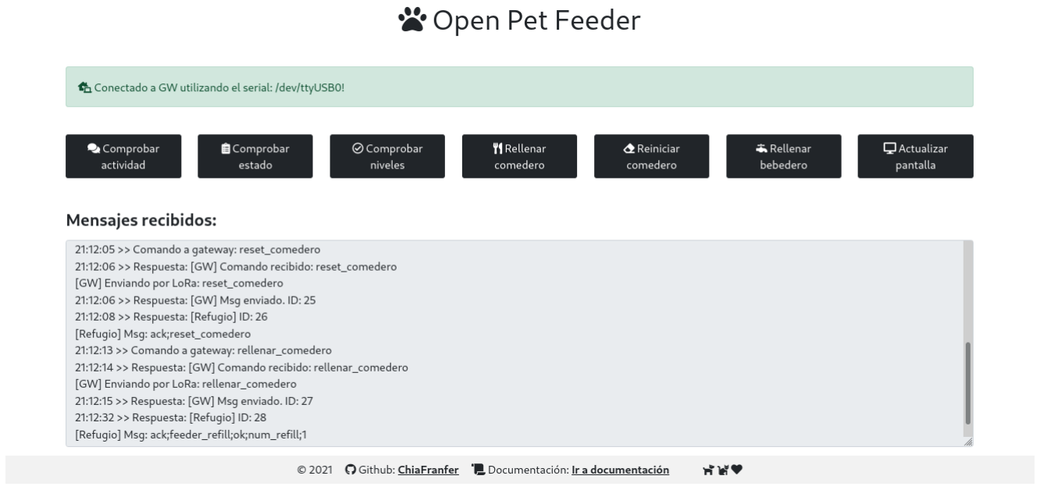
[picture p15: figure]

Figura 6: Captura de la web Open Pet Feeder, donde se muestra en la consola la interacción entre estación del campo y estación del refugio a través del comando reset comedero (botón Reiniciar comedero).

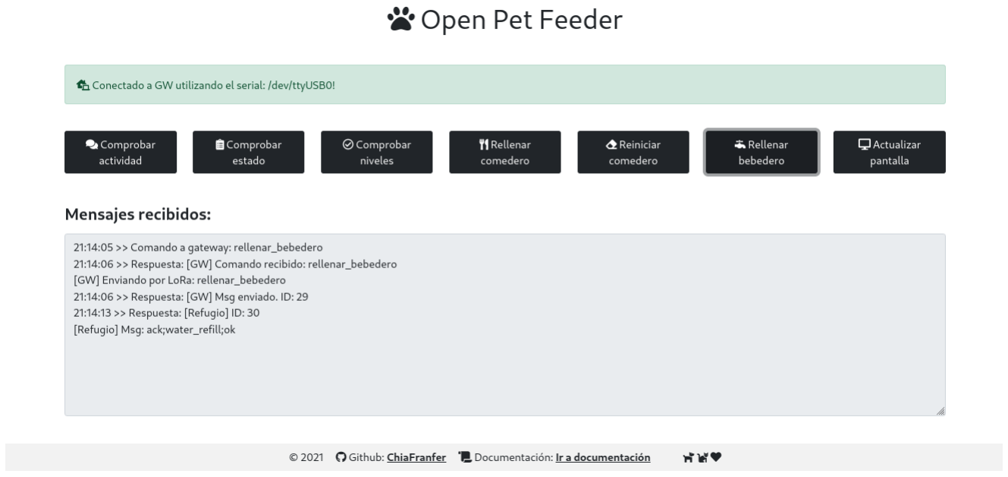
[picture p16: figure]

Figura 7: Captura de la web Open Pet Feeder, donde se muestra en la consola la interacción entre estación del campo y estación del refugio a través del comando rellenar bebedero (botón Rellenar bebedero).

El botón Actualizar pantalla (comando asociado update oled) no realiza la función que describe su nombre, ya que no se implementó a nivel arduino por ocupar más espacio del disponible en el arduino nano (la librería OLED ocupa bastante espacio). Si se envía este comando, la estación del refugio devuelve un string con “to do”, indicando que hay que implementarlo.

# Anexo

En este anexo, se incluye el código empleado para crear la web.

## Aplicación web: app.py

1 | import engineio
2 | from flask import Flask, render_template
3 | from flask_socketio import SocketIO
4 | from flask_serial import Serial
5 | from datetime import datetime

6
7 | import json
8 | import socketio
9 | import os

10
11 app = Flask(__name__)

12
13 | ## Configuration Serial GW
14 | serial_port = ’/dev/ttyUSB0’ | # Modificar aqui el serial del
Arduino, lo dice el IDE
15 | app.config[’SERIAL_PORT’] = serial_port
16 | app.config[’SERIAL_TIMEOUT’] = 0.1
17 | app.config[’SERIAL_BAUDRATE’] = 115200
18 | app.config[’SERIAL_BYTESIZE’] = 8
19 | app.config[’SERIAL_PARITY’] = ’N’
20 | app.config[’SERIAL_STOPBITS’] = 1

21
22 socketio = SocketIO(app, async_mode="gevent", ping_timeout=5, logger=False, engineio_logger=False)
23 ser = Serial(app)

24

25 | #
26 | # | Enpoints
27 | #

28
29 | # Endpoint home page
30 | @app.route("/")
31 | def index():
32 | # Comprobamos que el serial existe
33 | if os.path.exists(serial_port):
34 | serial_exists = True
35 | else:
36 | serial_exists = False

37
38 return render_template("index.html", serial_port=serial_port, serial_exists= serial_exists)

39
40 | # Endpoint documentation page
41 | @app.route("/doc")
42 | def doc():
43 | return render_template("doc.html")

44

45 | #
46 | # | SocketIO
47 | #

48
49 | # Handler SocketIO [messages of web]
50 | @socketio.on(’send’)
51 | def handle_send(json_str):
52 | data = json.loads(json_str)["message"]
53 | print("Boton pulsado: {}".format(data))

54
55 | # Enviamos por serial
56 | try:
57 | ser.on_send(data)
58 | except Exception as ex:
59 | print("Error on serial: {}".format(ex))

60
61 | # Enviamos en el socket ’receive_message’ [hacer en recepcion serial]
62 | now = datetime.now()
63 | msg = "{} >> Comando a gateway: {}".format(now.strftime(" %H: %M: %S"), data)
64 | socketio.emit("receive_message", data={"message":str(msg)})

65

66 | #
67 | # | Flask-Serial
68 | #

69
70 | # Handler incoming serial messages
71 | @ser.on_message()
72 | def handle_message(msg):
73 | try:
74 | print("receive message: {}".format(msg))
75 | now = datetime.now()
76 | msg = "{} >> Respuesta: {}".format(now.strftime(" %H: %M: %S"), msg.decode("utf-8").
| | strip(’\n’))
77 | print("Send socket msg: {}".format(msg))
78 | socketio.emit("receive_message", data={"message":str(msg)})
79 | except Exception as ex:
80 | print(ex)

81
82 | # Log thread serial
83 | @ser.on_log()
84 | def handle_logging(level, info):
85 | print(level, info)

86
87 | if __name__ == ’__main__’:
88 | socketio.run(app, debug=False, log_output=True)

89

## Página principal de la web: index.html

1 | <!doctype html>
2 | <html lang="es">
3 | <head>

4 | <!-- Required meta tags -->
5 | <meta charset="utf-8">
6 | <meta name="viewport" content="width=device-width, initial-scale=1">
7 | <link rel="icon" type="image/png" href="static/favicon.ico">

8
9 | <!-- Bootstrap CSS -->
10 | <link href="https://cdn.jsdelivr.net/npm/bootstrap@5.0.2/dist/css/bootstrap.min.css
" rel="stylesheet" integrity="sha384-EVSTQN3/ azprG1Anm3QDgpJLIm9Nao0Yz1ztcQTwFspd3yD65VohhpuuCOmLASjC" crossorigin="anonymous ">
11 <link rel="stylesheet" href="https://cdnjs.cloudflare.com/ajax/libs/font-awesome/5.15.3/css/all.min.css" integrity="sha512-iBBXm8fW90+nuLcSKlbmrPcLa0OT92xO1BIsZ +ywDWZCvqsWgccV3gFoRBv0z+8dLJgyAHIhR35VZc2oM/gI1w==" crossorigin="anonymous" referrerpolicy="no-referrer" />
12 <script src="https://cdn.socket.io/3.1.3/socket.io.min.js" integrity="sha384-cPwlPLvBTa3sKAgddT6krw0cJat7egBga3DJepJyrLl4Q9/5WLra3rrnMcyTyOnh" crossorigin=" anonymous"></script>
13 <script src="https://code.jquery.com/jquery-3.6.0.min.js" integrity="sha256-/xUj+3 OJU5yExlq6GSYGSHk7tPXikynS7ogEvDej/m4=" crossorigin="anonymous"></script>

14
15 | <title>Open Pet Feeder</title>
16 | </head>
17 | <body>
18 | <h1 style="text-align: center; margin-top: 2 %;"><a href="/" style="text-decoration:
none; color: inherit;"><i class="fas fa-paw"></i> Open Pet Feeder</a></h1>

19

20
21 <div class="container" style="margin-top: 3 %;">
22 { % if serial_exists == True %}
23 | <div class="alert alert-success" role="alert" style="margin-bottom: 3 %;">
24 | <i class="fas fa-laptop-house"></i> Conectado a GW utilizando el serial: {{
serial_port}}!
25 | </div>
26 | { % else %}
27 | <div class="alert alert-danger" role="alert" style="margin-bottom: 3 %;">
28 | <i class="fas fa-laptop-house"></i> No existe el serial ’{{serial_port}}’.
Configura el serial y reinicia el programa.
29 | </div>
30 | { % endif %}

31
32 | <div class="row" style="text-align: center;">
33 | <div class="col">
34 | <button type="button" class="btn btn-dark mt-1" id="send_ping" value="ping"><
i class="fas fa-comments"></i> | Comprobar actividad</button>
35 | </div>
36 | <div class="col">
37 | <button type="button" class="btn btn-dark mt-1" id="send_status" value="
status"><i class="fas fa-clipboard-list"></i> | Comprobar estado</button>
38 | </div>
39 | <div class="col">
40 | <button type="button" class="btn btn-dark mt-1" id="send_check_levels" value=
"check_levels"> <i class="far fa-check-circle"></i> | Comprobar niveles</button>
41 | </div>
42 | <div class="col">

43 | <button type="button" class="btn btn-dark mt-1" id="send_comedero" value="
rellenar_comedero"><i class="fas fa-utensils"></i> Rellenar comedero</button>
44 | </div>
45 | <div class="col">
46 | <button type="button" class="btn btn-dark mt-1" id="send_reset_comedero"
value="reset_comedero"><i class="fas fa-eraser"></i> Reiniciar comedero</button>
47 | </div>
48 | <div class="col">
49 | <button type="button" class="btn btn-dark mt-1" id="send_bebedero" value="
rellenar_bebedero"><i class="fas fa-faucet"></i> Rellenar bebedero</button>
50 | </div>

51
52 | <div class="col">
53 | <button type="button" class="btn btn-dark mt-1" id="send_oled" value="
update_oled"><i class="fas fa-desktop"></i> Actualizar pantalla</button>
54 | </div>
55 | </div>
56 | </div>

57
58 | <div class="container" style="margin-top: 3 %;">
59 | <div class="console">
60 | <label class="form-label" for="receive"> <h4> <b>Mensajes recibidos:</b> </h4
> | </label>
61 | <textarea readonly class="form-control" name="receive" id="receive" rows="8"
style="width: 100 %; height: auto;"></textarea>
62 | </div>
63 | </div>

64
65 | <!-- Footer -->
66 | <div class="footer fixed-bottom mt-4 py-4">
67 | <div class="text-center p-2" style="background-color: rgba(0, 0, 0, 0.05);
margin-bottom: -1 %;">
68 | C | 2021 | <i class="fab fa-github" style="margin-left: 1 %;"></i> Github:
69 | <a class="text-reset fw-bold" href="https://github.com/ChiaFranfer">
ChiaFranfer</a>
70 | <i class="fas fa-scroll" style="margin-left: 1 %;"></i> Documentacion: <a
class="text-reset fw-bold" href="{{url_for(’doc’)}}"> Ir a documentacion</a>
71 | <i class="fas fa-dog" style="margin-left: 3 %;"></i> <i class="fas fa-cat"></i
> <i class="fas fa-heart"></i>
72 | </div>
73 | </div>

74
75 | <script src="https://cdn.jsdelivr.net/npm/bootstrap@5.0.2/dist/js/bootstrap.
bundle.min.js" integrity="sha384-MrcW6ZMFYlzcLA8Nl+ NtUVF0sA7MsXsP1UyJoMp4YLEuNSfAP+JcXn/tWtIaxVXM" crossorigin="anonymous"></script >
76 | <script type="text/javascript" charset="utf-8">
77 | $(document).ready(function() {
78 | var socket = io.connect(’http://’ + document.domain + ’:’ + location.port);

79
80 | $(’#send_status’).on(’click’, function() {
81 | var message = $(this)[0].value;
82 | console.log(’Enviando: ’ + message);
83 | var data = ’{’ + ’"message": "’ + message + ’"}’;

84 | socket.emit(’send’, data=data);
85 | });

86
87 | $(’#send_ping’).on(’click’, function() {
88 | var message = $(this)[0].value;
89 | console.log(’Enviando: ’ + message);
90 | var data = ’{’ + ’"message": "’ + message + ’"}’;
91 | socket.emit(’send’, data=data);
92 | });

93
94 | $(’#send_reset_comedero’).on(’click’, function() {
95 | var message = $(this)[0].value;
96 | console.log(’Enviando: ’ + message);
97 | var data = ’{’ + ’"message": "’ + message + ’"}’;
98 | socket.emit(’send’, data=data);
99 | });

100
101 | $(’#send_comedero’).on(’click’, function() {
102 | var message = $(this)[0].value;
103 | console.log(’Enviando: ’ + message);
104 | var data = ’{’ + ’"message": "’ + message + ’"}’;
105 | socket.emit(’send’, data=data);
106 | });

107
108 | $(’#send_bebedero’).on(’click’, function() {
109 | var message = $(this)[0].value;
110 | console.log(’Enviando: ’ + message);
111 | var data = ’{’ + ’"message": "’ + message + ’"}’;
112 | socket.emit(’send’, data=data);
113 | });

114
115 | $(’#send_check_levels’).on(’click’, function() {
116 | var message = $(this)[0].value;
117 | console.log(’Enviando: ’ + message);
118 | var data = ’{’ + ’"message": "’ + message + ’"}’;
119 | socket.emit(’send’, data=data);
120 | });

121
122 | $(’#send_oled’).on(’click’, function() {
123 | var message = $(this)[0].value;
124 | console.log(’Enviando: ’ + message);
125 | var data = ’{’ + ’"message": "’ + message + ’"}’;
126 | socket.emit(’send’, data=data);
127 | });

128
129 | socket.on(’receive_message’, function(data){
130 | console.log(data);
131 | var text = data[’message’];
132 | var $textarea = $(’#receive’);
133 | $textarea.val($textarea.val() + text + ’\n’);
134 | $textarea.scrollTop($textarea[0].scrollHeight);
135 | })
136 | });

138 | </script>
139 | </body>
140 | </html>

141

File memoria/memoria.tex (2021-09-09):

\documentclass[12pt]{article}
\usepackage[spanish, english, es-tabla]{babel}
\usepackage[utf8]{inputenc}
\usepackage{amsmath,amssymb}
\usepackage{graphicx}
\usepackage{gensymb}
\usepackage{outlines}
\usepackage[export]{adjustbox}
\usepackage{adjustbox}
\usepackage{multicol}
\usepackage{lipsum}
\parskip 1ex

\usepackage{eurosym}

% add code
\usepackage{listings}

\usepackage{array}

% text font 

\usepackage{courier}

%\usepackage{fontspec}

\usepackage[dvipsnames]{xcolor}

\usepackage{hyperref}
\usepackage{subcaption}
\usepackage[left = 2cm, right = 2cm, bottom = 2cm, top = 3cm]{geometry}

\hypersetup{
	colorlinks=true,
	linkcolor=black,
	%filecolor=magenta,      
	urlcolor=cyan,
}

\hypersetup{
	pdftitle= {Diseño y automatización de un sistema de alimentación OpenSource para animales a través de la tecnología LoRa},
	pdfauthor = {Lucía Francoso Fernández},
	pdfsubject = {Electrónica y comunicaciones móviles},
	pdfkeywords = {Arduino, LoRa, automatización, LoRaWAN, punto a punto, OpenSource}
}

% define color for C code (Anexos)

\definecolor{codegreen}{rgb}{0,0.6,0}
\definecolor{codegray}{rgb}{0.5,0.5,0.5}
\definecolor{codepurple}{rgb}{0.58,0,0.82}
\definecolor{backcolour}{rgb}{0.95,0.95,0.92}

\lstdefinestyle{mystyle}{
	backgroundcolor=\color{backcolour},   
	commentstyle=\color{codegreen},
	keywordstyle=\color{magenta},
	numberstyle=\tiny\color{codegray},
	stringstyle=\color{codepurple},
	basicstyle=\ttfamily\footnotesize,
	breakatwhitespace=false,         
	breaklines=true,                 
	captionpos=b,                    
	keepspaces=true,                 
	numbers=left,                    
	numbersep=5pt,                  
	showspaces=false,                
	showstringspaces=false,
	showtabs=false,                  
	tabsize=2
}

\lstset{style=mystyle}

% https://tex.stackexchange.com/questions/60209/how-to-add-an-extra-level-of-sections-with-headings-below-subsubsection
\newcommand{\subsubsubsection}[1]{\paragraph{#1}\mbox{}\\}
\setcounter{secnumdepth}{4}
\setcounter{tocdepth}{4}

%%ENCABEZADO Y PIE DE PAGINA

\usepackage{fancyhdr}
\fancyhf{}
\lhead[\leftmark]{\small TFE: Lucía Francoso}
\rhead[Nombre Autor]{\rightmark}
\cfoot[\thepage]{}
\cfoot[]{\thepage}
\renewcommand{\headrulewidth}{0.5pt}
\renewcommand{\footrulewidth}{0pt}
\fancypagestyle{plain}{
	\fancyhf{}
	\fancyhead[L]{}
	\fancyfoot[C]{\thepage}
	\renewcommand{\headrulewidth}{0pt}
	\renewcommand{\footrulewidth}{0pt}
}
\pagestyle{fancy}

\begin{document}
	\selectlanguage{spanish}
	
	%\thispagestyle{empty}

	%\pagebreak
	
	\thispagestyle{empty}
	
	\newgeometry{left=0.01cm,bottom=0.01cm, top=0.01cm}
	
	%width=0.3\textwidth,
		
	%\begin{figure}[h!]
	%	\includegraphics[height=\textheight,left]{img/banda_etsit_90.png}

%	\end{figure}

	\begin{minipage}{0.2\textwidth}
		
	\end{minipage}
	\centerline{\begin{minipage}[t][5cm][b]{0.5\textwidth}
		%	\textbf{UNIVERSIDAD POLITÉCNICA DE} \\
			
		%	\textbf{CARTAGENA}\\
			
			\title{\textbf{Automatización y control de bebederos automáticos para especies animales usando LoRa}} 
			\maketitle
			
			\vspace{0.5cm}
			
			\hspace{1.5cm} \textbf{TRABAJO FIN DE GRADO} \\
			
			\vspace{0.5cm}
			
			\hspace{1.3cm} Grado en Ingeniería en Sistemas  de\\
			
			\vspace{0.01cm}
			
			\hspace{2.7cm} Telecomunicaciones \\
			
			\vspace{1cm}
			
			\textbf{Autora:}\author{ Lucía Francoso Fernández}\\
			
			\textbf{Tutor:} Juan Pascual García
		\end{minipage}}

	\restoregeometry
	
	\pagebreak
	
	\tableofcontents
	
	\pagebreak

	\listoffigures
	\addcontentsline{toc}{section}{Índice de figuras}
	
	\pagebreak
	
	\listoftables
	\addcontentsline{toc}{section}{Índice de tablas}
	
	\pagebreak
	
	\section*{Agradecimientos}
	\thispagestyle{plain}
	\addcontentsline{toc}{section}{Agradecimientos}
	
	\noindent Primero, me gustaría agradecer a mi tutor, Juan Pascual García, por aceptar este reto junto a mi, y apoyarlo en todo momento. Fue un proyecto diferente, algo arriesgado, y siempre confió en que lo sacaríamos hacia delante. Muchas gracias por tu apoyo a distancia, debido a la Covid-19, que a pesar de todo siempre he obtenido tu ayuda y tu feedback a tiempo, y confianza en todo proceso requerido en este proyecto, pilares fundamentales en cualquier emprendimiento.\\
	
	\noindent Me gustaría, además, agradecer a mi familia, en especial a mis padres, Francisco y María Dolores, ya que es difícil entender que decida estar un año sin apenas créditos matriculados, la importancia de aprender de manera complementaria a la universidad, de buscar (y encontrar) aquello que me gusta dentro de esta carrera que, a pesar de las dificultades, siento que no podría haber elegido otra mejor. Sin ese apoyo, todo habría sido mucho más difícil, y siendo mi situación poco común, agradezco que lo hayan comprendido. A esto se suma su aportación económica, sin ella no habría podido realizar este proyecto, el cual he sentido en todo momento muy personal y muy bueno para mi, en tanto a nivel profesional, como personal como para la protectora que será beneficiaria de este dispositivo. Agradecer a mis hermanas Isabel y Claudia, que a pesar de las diferencias, y a pesar de ser la mayor, tienden a reforzarme en los momentos difíciles, recalcando mis virtudes; confiaron en este proyecto, y saben lo bueno que podría conllevar, ya que han venido innumerables veces conmigo al refugio, al igual que mi padre.\\
	
	\noindent También agradecer al resto de mi familia, que en la distancia también me apoyan. En especial a mi tía Bárbara, que siempre me llama para darme ánimos con todo lo que hago y que confía en mi desde siempre. A mis primas Sonia y María, y a mi abuela Guadalupe, las cuales son ejemplos de mujeres admirables en mi familia y a las que quiero muchísimo. Especial mención a mi abuela, Lucía Figueredo, la cual falleció el año pasado y sé que estaría muy orgullosa de ver a su nieta convertirse en ingeniera, y creando este proyecto. \\
	
	\noindent Debo agradecer también a mis suegros, Encarnación y Miguel Ángel, por dedicarme parte de su tiempo siempre que pueden, y en especial, en el desarrollo del prototipo exterior; agradezco enormemente que me hayan prestado sus herramientas, ya que sin ellas el resultado no habría sido el mismo. Muchas gracias por permitirme instalar en vuestra casa el otro extremo de la comunicación, que ha permitido poder concebir este proyecto. \\
	
	\noindent Me gustaría también agradecer a mi amiga Magdalena, mi amiga de toda la vida, la cual me apoya incondicionalmente, y me inspira en su lucha constante por mejorarse así misma y por ganarse la vida en lo que más le gusta, la música. A mi amiga Clara, la cual es una estupenda teleco, que siempre ha confiado en mi más que yo misma, y la cual me inspira por ser una persona fuerte, independiente y que tiene claro lo que quiere. A mi amigo Pablo, porque ni la distancia ni las exigentes carreras que cursamos nos han hecho perder el contacto, ni perder un vínculo que hace años se formó. Es un placer poder contar con estar tres personas.\\  
	
	\pagebreak
	\thispagestyle{plain}
	
	\noindent Especial mención a mi compañero Enrique Fernández Sánchez, el cual ha sido también como mi tutor, ayudándome muchísimo a comprender la importancia del Open Source, guiándome en el conocimiento sobre microcontroladores y LoRa, y en general, aconsejándome en todo lo que ha podido y más. Gracias a él, la introducción al mundo maker se me ha hecho más sencilla, mucho más consciente y sin excesivos agobios. A esto, añadir que su aportación económica me ha ayudado muchísimo a sacar este proyecto hacia delante. Sin duda, ajeno a este proyecto, aprenderé muchas cosas de él y gracias a él, y no me cabe la menor duda de que es un gran teleco y una gran persona.\\
	
	\noindent Agradecer a Patitas Unidas Los Alcázares por permitirme instalar un dispositivo en sus instalaciones, y por comprender mi ausencia durante algunos meses donde el desarrollo de este proyecto era muy exigente. Especial mención a mi compañera Jen, con la que voy al refugio prácticamente siempre; sus ganas y actitud al tratar con los perros desde luego es una cualidad a admirar, y es una inspiración que recarga fuerzas para seguir luchando por los animales.\\
	
	\noindent Por último, agradecer a todas esas personas que han publicado su proyecto,  documentación y dejan todo ese desarrollo bajo licencias Open Source, permitiendo que gente como yo desarrolle su proyecto basándome en sus librerías, o me den ideas que sin duda impulsen el mío. Estarán debidamente mencionadas, ya que merecen ese crédito.\\
	
	\pagebreak
	
	\section[Introducción]{Introducción} %corchetes, marcapaginas, llaves, texto
	
	Tras finalizar los estudios de grado en ingeniería en sistemas de telecomunicaciones, se requiere como último paso para la obtención del título la elaboración del \textit{Trabajo Fin de Grado} (TFG). 
	El TFG como tal tiene unos objetivos claros, los cuales son demostrar que se han adquirido las competencias básicas intrínsecas al grado, y que el alumno es capaz de seguir aprendiendo a partir de los conocimientos ya obtenidos, innovar, desenvolverse ante un problema determinado y, en resumen, saber llevar a cabo una investigación o proyecto que tenga como objetivo la resolución de dicho problema. \\
	
	\noindent En este documento, se recoge el proyecto realizado como TFG,  el cual va en línea con la filosofía y objetivos del \textit{Trabajo Fin de Grado} en sí mismo. Se detallará el proceso de creación de un sistema de alimentación para animales automatizado, donde se monitorizan de manera remota el estado de los tanques de reserva de agua y pienso. Así, se pretende exponer el conjunto de elementos hardware y software que serán necesarios para monitorizar, automatizar y acceder a ciertos datos de forma remota empleando, principalmente, Arduino y LoRa.\\

	\subsection[Contexto y justificación del trabajo]{Contexto y justificación del trabajo}
	\label{subsection: contexto y justificacion}
	
	\noindent Este proyecto ha sido concebido con el objetivo principal de ayudar a la preservación de la vida animal, ante el aumento de especies en extinción, sobre todo en lo que llevamos de siglo [\ref{bib: enlace National Geographic}]-[\ref{bib: enlace Fundación AQUAE}], 
	y ante el hecho de que miles de animales domésticos siguen siendo abandonados al año en España [\ref{bib: enlace Fundación Affinity}]-[\ref{bib: enlace RTVE}]. \\ %\footnotemark. \\
	
	%Fundación Affinity, 20 minutos, La Razón, RTVE
	%\footnotetext{\href{https://www.fundacion-affinity.org/observatorio/infografia-el-nunca-lo-haria-estudio-de-abandono-y-adopcion-2020}{Fundación Affinity}, \href{https://www.20minutos.es/noticia/4318383/0/el-abandono-animal-en-espana-aumenta-un-25-en-las-ultimas-semanas/}{20 minutos}, \href{https://www.larazon.es/medio-ambiente/20201118/qxv6yuokargfbnjvknn6bhm4ze.html}{La Razón}, \href{https://www.rtve.es/noticias/20200608/abandonos-animales-domesticos-se-han-disparado-espana-durante-meses-confinamiento/2015761.shtml}{RTVE}}

	\noindent Es por ello que se requiere de ayuda activa para paliar estos problemas. Las tareas de carácter solidario, en bastantes casos, no siempre cuentan con suficientes voluntarios; además, siendo un problema tan extendido y avanzado, el número de acciones que hay que llevar a cabo para aliviarlo es alto para un número limitado de voluntarios, los cuales deben incrementar considerablemente el tiempo que pasan realizando este tipo de tareas. 
	Tanto si se trata de un refugio de animales domésticos abandonados, como de reservas naturales donde se intenta repoblar una especie, los animales dependen enteramente del trabajo de los voluntarios. Así pues, es de vital importancia la optimización de las tareas de voluntariado, su automatización e, incluso, control remoto, mediante la creación de herramientas que ayuden a reducir el tiempo que se destina a tareas rutinarias para poder utilizar ese tiempo a otras tareas (de rescate, o de financiación para el mantenimiento de las instalaciones y de los propios animales, por ejemplo). \\
	
	\noindent Con el objetivo en mente de ayudar a la preservación de la fauna (y con ello, de la vida de los ecosistemas terrestres), evitando la extinción de especies y el abandono animal, se ha concebido y desarrollado este proyecto teniendo en cuenta los diferentes casos de uso (emplazamientos donde se podrá instalar el sistema, características del entorno), mejor adaptación a ellos, relación entre buenas prestaciones y bajo consumo, precio total del producto, o facilidad de uso por parte de un usuario medio. Es por ello que desde el principio se propone una serie de actuaciones a realizar, acorde a lo anteriormente mencionado, tales como: \\
	
	\begin{itemize}
		\item El diseño del sistema de alimentación será tal que el producto final pueda ser instalado no sólo en hogares, sino en sitios remotos, donde el acceso a recursos tales como la electricidad o Internet son escasos o inexistentes. Así pues, el dispositivo utilizará energía solar y baterías recargables, comunicación de bajo consumo y largo alcance y modo de ahorro de energía. 
		\item El dispositivo final no será pesado ni voluminoso, facilitando así tanto su transporte como su manejo. No se dejará que los dispositivos electrónicos queden al alcance de los animales; de este modo se evitará que los animales puedan sufrir daño (o viceversa), y posibles problemas de humedad presentes en el entorno; se usarán protecciones adecuadas a la calidad de los componentes del dispositivo.
		\item El dispositivo contará con una pantalla OLED que permitirá ver a la persona que esté físicamente delante de él si funciona correctamente. También se permitirá el acceso a datos a personas interesadas que quieran consultarlos de manera remota.

	\end{itemize}

	\subsubsection[Caso de aplicación]{Caso de aplicación}
	
		Nuestro caso de aplicación será el entorno donde se desea situar uno de estos dispositivos para validar su funcionamiento, que en este caso se trata del refugio perteneciente a la protectora Patitas Unidas Los Alcázares, situado en el término municipal de Torre Pacheco (Murcia).
	La elección de esta ubicación se fundamenta en una serie de razones:
	
	\begin{itemize}
		\item Al ser voluntaria para esta protectora, conozco bien sus necesidades, es decir, qué puede ser de utilidad para la protectora en el refugio y qué soluciones se han probado para determinados problemas que han ido surgiendo; además, conozco bajo qué condiciones climáticas es vulnerable y qué necesidades esporádicas emergen bajo dichas condiciones. Teniendo en cuenta la zona geográfica donde se ubica (Murcia), y los años de experiencia en el refugio, se ha detectado una problemática que se manifiesta durante  periodos continuados de lluvias (lluvias torrenciales, DANA, gota fría), la cual consiste en la inundación de las zonas colindantes al refugio, inclusive carreteras de acceso, lo que impide llegar a él (cierre de carreteras, niveles altos de riesgo por precipitación, o el simple hecho de contar con grandes volúmenes de agua en la carretera que impiden la circulación segura por la vía). Es por ello que, mediante el desarrollo de este proyecto, se pretende ofrecer una solución que palie las consecuencias de no poder llegar al refugio bajo esas circunstancias, como es la alimentación de los animales.
		\item Se trata de un entorno sin electricidad y sin internet. Desarrollar un proyecto y probarlo en este tipo de entorno nos ayudará a la hora de extrapolarlo a otros emplazamientos donde la ausencia de este tipo de recursos supone también una limitación y un aspecto a tener en cuenta para definir y desarrollar el proyecto en sí mismo.
		\item Se puede establecer un enlace punto a punto, ya que se puede dejar fijo un equipo transmitiendo o recibiendo que, además, se conecte a internet (ya que es un recurso disponible) para cargar datos que reciba del otro extremo a un servidor conocido. Un equipo estará presente en el refugio y el otro en una casa con internet y electricidad; esto significa que al menos este extremo será más controlable, y será este extremo el que subirá datos a la nube. Nos tendremos que preocupar más del otro extremo, donde no tendremos electricidad ni internet y donde situaremos los sensores que recogerán datos y realizarán la automatización.
	\end{itemize}
	
	\subsection[Objetivos del trabajo]{Objetivos del trabajo}
	\label{subsection: objetivos del trabajo}
	El objetivo principal del presente proyecto es el diseño de un sistema de alimentación para animales que permita la monitorización de los niveles de agua y pienso que se encuentran en reservas, las cuales rellenan un bebedero y un comedero, respectivamente.  Con ello, se pretende automatizar el proceso de alimentación de animales, además del uso de la tecnología LoRa para tener acceso al estado del sistema de forma remota. Así pues, se pretende:
	
	\begin{itemize}
		\item Realizar una aproximación a la tecnología LoRa.
		\item Diseñar el sistema de alimentación para animales.
		\item Realizar tanto simulaciones para el enlace LoRa que se creará entre transmisor y receptor, como cálculos teóricos que determinen si el enlace es posible.
		\item Construir el prototipo y probarlo en entorno controlado y, posteriormente, en entorno real.
		\item Crear una plataforma de representación de datos.
	\end{itemize}
	
	\subsection[Enfoque y método seguido]{Enfoque y método seguido}
	
	\noindent En primer instancia, como aclaración, decir que se trata de un trabajo académico, por lo que se prioriza el aprendizaje y la aplicación de lo aprendido. Es decir, partiendo de que los objetivos del proyecto están definidos, se requiere una investigación continuada y su aplicación al diseño del sistema de todas las partes que conformarán el proyecto en su totalidad (tanto para la consecución de dichos objetivos como para establecer unas bases para futuros proyectos). Así, conocer el entorno Arduino y la tecnología LoRa es fundamental, y por ello, será lo que mayor tiempo requiera en términos de estudio y aplicación. \\
	
	\noindent En tanto al método seguido, decir que se ha separado en bloques temáticos; se investiga cada bloque por separado (búsqueda y recopilación de información), y se prueba (diseño y simulaciones, en software y hardware). Posteriormente, siguiendo una metodología en cascada, una vez resueltos los bloques individuales, se unen los bloques formando un prototipo y se prueba en conjunto. En resumen, a lo largo del trabajo se profundizará en cada uno de los bloques tal que se estudiarán las tecnologías, se analizarán los requisitos y se procederá a la búsqueda de soluciones que permitan resolver cada bloque de manera individual, y por consiguiente, la interconexión entre ellos. \\
	
	\noindent Finalmente, enunciamos cada bloque y lo describiremos brevemente para mayor claridad:
	
	\begin{itemize}
		\item \textbf{Monitorización:} se emplearán sensores en las reservas del sistema de alimentación.
		\item \textbf{Control: }microcontrolador que implementa la lógica del sistema.
		\item \textbf{Comunicaciones: }módulo LoRa.
		\item \textbf{Actuación: } control sobre posible bomba de agua y reserva de comida.
		\item \textbf{Alimentación autónoma:} posible uso de baterías recargables.
	\end{itemize}
	
	%\noindent Todo esto puede variar ligeramente respecto a lo inicialmente aquí expuesto, según se profundice en cada bloque y se adquieran mayores conocimientos.
	
	\subsection[Planificación del trabajo]{Planificación del trabajo}
	
	\noindent En el \hyperref[anexo II: presupuesto]{Anexo II}, se adjunta una tabla resumen, elaborada durante el proceso de concepción del proyecto (etapa inicial), de manera que, por una parte, se pudiera tener una idea de los recursos necesarios para poder dar comienzo al proyecto (tanto materiales como software); por otra parte, serviría, a grosso modo, para conocer y planificar una serie de pasos desde esa concepción hasta una presentación de un prototipo funcional, resultado del desarrollo del proyecto. 
	
	\subsection[Breve sumario de productos obtenidos]{Breve sumario de productos obtenidos}
	
	\noindent Siendo el objetivo fundamental de este proyecto el diseño del sistema de alimentación, su construcción y la realización de las pruebas necesarias del prototipo construido, mostramos un desglose de los productos resultantes que se espera obtener:
	
	\begin{itemize}
		\item \textbf{Prototipo hardware} específico para el sistema de alimentación, perfectamente operativo.
		\item \textbf{Software} apto para el control y monitorización del sistema creado.
		\item \textbf{Memoria} del proyecto, donde se justifica toda la elaboración del mismo. 
		\item \textbf{Video demostración de las pruebas realizadas}, tomado en un entorno real donde se pueda observar que la comunicación LoRa se establece sin problema.
		\item \textbf{Presentación} del proyecto para exposición de las ideas fundamentales y los resultados obtenidos de este proyecto.
	\end{itemize}
	
	\noindent Además, se ampliará el alcance del proyecto creando un repositorio en \textit{GitHub }(\url{https://github.com/}), donde se incluirá todo el desarrollo de este proyecto (\url{https://github.com/ChiaFranfer/open-pet-feeder}), permitiendo así que otras personas puedan usarlo o mejorarlo.
	
	\pagebreak
	
	\subsection[Breve descripción de los capítulos restantes de la memoria]{Breve descripción de los capítulos restantes de la memoria}
	
	\noindent Este documento está compuesto por 5 capítulos:
\\
	
	\noindent \textbf{Capítulo 1: }contextualización del problema y aproximación a una solución. Se muestra, además, la planificación seguida para el proyecto, finalizando con la descripción de resultados o productos obtenidos.\\
	
	\noindent \textbf{Capítulo 2: }estudio del estado actual del ámbito del tema del proyecto. También, se presentan ejemplos Open Source dentro de este ámbito.\\
	
	\noindent \textbf{Capítulo 3:} este es el capítulo principal del proyecto, donde se explicará todo el proceso de diseño del sistema. Se parte de la determinación de las funcionalidades que hay que cubrir, para determinar posibles necesidades y así iniciar una búsqueda de soluciones. Es aquí donde se exponen tanto las tecnologías empleadas en el diseño de la solución (Arduino y LoRa), como distintos componentes hardware necesarios para cada funcionalidad. Finalmente, se expone la elección de soluciones hardware, y se define un primer prototipo provisional. Se plantea un primer prototipo y las pruebas necesarias para verificar su correcto funcionamiento, tanto en monitorización como en comunicaciones. \\
	
	\noindent \textbf{Capítulo 4: }se trata el proceso de construcción del prototipo definitivo, sus evoluciones desde el prototipo provisional y las pruebas realizadas para verificar su funcionamiento, incluyendo el contexto real (entorno definitivo).\\
	
	\noindent \textbf{Capítulo 5:} se muestran los resultados y las conclusiones obtenidas, tanto en el proceso de diseño como a la finalización del proyecto. También se proponen posibles líneas de investigación futuras con las que se puede mejorar el diseño.\\

	\pagebreak

	\section[Estado del arte]{Estado del arte}  
	
	\noindent En este capítulo expondremos la situación actual en el ámbito del control y automatización de sistemas de alimentación para animales (dentro del marco Open Source). Además, se comentarán otros proyectos relacionados con este ámbito y ejemplos que emplean las tecnologías Arduino y/o LoRa.
	
	\subsection[Contexto actual]{Contexto actual}
		
	\noindent Existen muchos proyectos Open Source relacionados con la alimentación automática o semiautomática de animales domésticos, principalmente gatos y perros. Sin embargo, no existen (o al menos, no se han encontrado) proyectos que usen LoRa como tecnología radio, sino que emplean la red local WiFi del hogar donde se sitúe el dispositivo de alimentación; es decir, se trata de entornos con electricidad e internet, y no del entorno en el que trabajará nuestro proyecto. \\
	
	\noindent A pesar de ello, se ha visualizado este tipo de proyectos y tenido en cuenta para el desarrollo del prototipo en tanto a apariencia externa, facilidad de uso, eficiencia de los componentes, o, incluso, opciones para mover el pienso desde la reserva hasta el comedero del animal, o el agua desde la reserva hasta el bebedero. No se realizará comparativa con dispositivos autónomos comerciales de alimentación para animales, ya que se pretende elaborar un proyecto Open Source, que nada tiene que ver con soluciones comerciales propietarias; además, los objetivos de este proyecto (principalmente establecer unas bases para investigar sobre este tipo de dispositivos que ayudan a animales y voluntarios), requerimientos y tecnologías empleadas son totalmente diferentes. \\
	
	\noindent Aunque se hablará con más detalle en la sección \ref{Sección 3: Diseño del sistema}, en el momento de elaborar la planificación para este proyecto, se tuvo que preconcebir una serie de pasos a seguir. Es en el momento de la concepción del proyecto, mientras se realiza la planificación, cuando se realizó una primera búsqueda de proyectos Open Source, tanto relacionados con alimentación autónoma de animales, como monitorización por LoRa de proyectos y alimentación autónoma de los mismos. No se centró la búsqueda en el primer tema exclusivamente, ya que, como hemos comentado, no se han encontrado proyectos que engloben alimentación autónoma para animales, monitorización por LoRa y alimentación autónoma del dispositivo.\\
	
	\subsubsection{Ejemplos de proyectos Open Source}
	
	\noindent A continuación, se comentarán brevemente algunos ejemplos de proyectos Open Source, relacionados con los tópicos que se han enumerado anteriormente y que, en opinión propia, merecen reconocimiento por la gran labor de investigación y divulgación que han realizado con dichos proyectos. 
	
	\pagebreak
	
	\subsubsubsection{Relacionados con alimentación autónoma de animales}
	
	\noindent A través de la plataforma \href{https://www.thingiverse.com/}{\textit{Thingiverse}}[\ref{bib: thingiverse web}], son varios los usuarios que han compartido sus creaciones relacionadas con alimentación autónoma de animales. Destacaremos al usuario \href{https://www.thingiverse.com/kitlaan/designs}{kitlaan}[\ref{bib: thingiverse kitlaan}], con su dispensador automático de pienso para gatos (\href{https://www.thingiverse.com/thing:27854}{\textit{Auger-based Cat Feeder}}[\ref{bib: thingiverse helices comedero}]). Con este proyecto, este usuario, entre otros, facilita los archivos de impresión en 3D que usó para construir su dispensador de pienso; documenta su proyecto, especificando las piezas que usa y que no son impresas, así como un vídeo del funcionamiento del dispensador.
	
	\subsubsubsection{Relacionados con monitorización de proyectos por LoRa}
	
	\noindent El usuario \href{https://create.arduino.cc/projecthub/xreef}{xreef}[\ref{bib: xreef user}], Renzo Mischianti, liberó uno de sus proyectos sobre monitorización vía LoRa, llamado \href{https://create.arduino.cc/projecthub/xreef/lora-e32-for-arduino-esp32-or-esp8266-specs-and-base-use-804d25}{\textit{LoRa E32 for Arduino, ESP32 or ESP8266: Specs and Base Use}}[\ref{bib: xreef project}]. En este proyecto, prueba el transceptor LoRa E32-TTL-100 con dos microcontroladores, el microcontrolador Wemos D1 mini (ESP8266), y el Arduino Uno. Libera las conexiones y los sketches que emplea para probar dichos microcontroladores, así como una \href{https://github.com/xreef/LoRa_E32_Series_Library}{librería}[\ref{bib: xreef library}] de elaboración propia para el E32-TTL-100, sin la cual la comunicación entre microcontrolador en transmisión y microcontrolador en recepción sería imposible (o deberíamos crearla nosotros).
	
	\subsubsubsection{Relacionados con alimentación autónoma de dispositivos}
	
	\noindent Para este tópico, se han visualizado muchos proyectos a través de YouTube, y vídeos explicativos de opciones de alimentación autónoma de dispositivos. 
	Se han visualizado asiduamente vídeos de los creadores \href{https://www.youtube.com/channel/UC6mIxFTvXkWQVEHPsEdflzQ}{\textit{GreatScott!}}[\ref{bib: canal greatScott}] y \href{https://www.youtube.com/channel/UCu7_D0o48KbfhpEohoP7YSQ}{\textit{Andreas Spiess}}[\ref{bib: canal andreas}], aunque no han sido los únicos. Un proyecto que me gustaría remarcar, ya que fue de los primeros que me impulsaron a realizar este proyecto, es el de \href{https://www.youtube.com/watch?v=2YJHcGQnpAk}{Automating a Greenhouse with LoRa! (Part 1)}[\ref{bib: video invernadero}], del creador \textit{GreatScott!}. En este proyecto no solo se usa LoRa para monitorizar un invernadero, sino que se hace uso de paneles solares para alimentar el proyecto. 
	
	\subsubsection{Determinación del tipo de TFG}
	
	\noindent Por último, es importante comentar que este TFG está catalogado como \textit{TFE Específico de Aprendizaje}; según la normativa sobre TFG específico de aprendizaje: \textit{``aquellos TFE específicos ligados a la consecución de los Objetivos de Desarrollo Sostenible (ODS) a través de la vinculación de manera directa a una solicitud de servicio, a desarrollar por el estudiante en su TFE, realizada por una asociación o institución externa, sin ánimo de lucro''}. Esto es así, ya que:
	
	\begin{itemize}
		\item Cumple el Objetivo 15 de Desarollo Sostenible (ODS), el cual trata de \textit{``Gestionar sosteniblemente los bosques, luchar contra la desertificación, detener e invertir la degradación de las tierras, detener la pérdida de biodiversidad''} [\ref{bib: ods}]. Con este proyecto, nos estamos enfocando en ayudar en la detención de la pérdida de biodiversidad, ya que, como se ha comentado anteriormente, se va a crear un dispositivo capaz de alimentar y abrevar animales en lugares sin electricidad y sin conexión a internet, usando el menor número de dispositivos radio posible (siendo estos de largo alcance y bajo consumo). Instalando estos dispositivos en zonas de cuidado de animales podemos reducir el tiempo que dedican los voluntarios a las diferentes actividades (como hemos mencionado en el apartado \ref{subsection: contexto y justificacion}), permitiendo usar ese tiempo en otras actividades igualmente prioritarias pero que difícilmente se pueden realizar en remoto, como el salvamento o rescate de animales, ubicación, repoblación o cuidados veterinarios. 
		\item Existe una solicitud formal de la protectora que va a hacer uso del dispositivo creado con este proyecto (ver Figura \ref{fig: estado del arte logos}), Patitas Unidas Los Alcázares [\ref{bib: fb patitas}] [\ref{bib: web patitas}]. Dicha solicitud recoge los mínimos que debe tener en cuenta el proyecto, ya expuestos en el apartado \ref{subsection: objetivos del trabajo}.
	\end{itemize}
	
	\begin{figure} [h!]
		\begin{center}
			\begin{tabular}{cc}
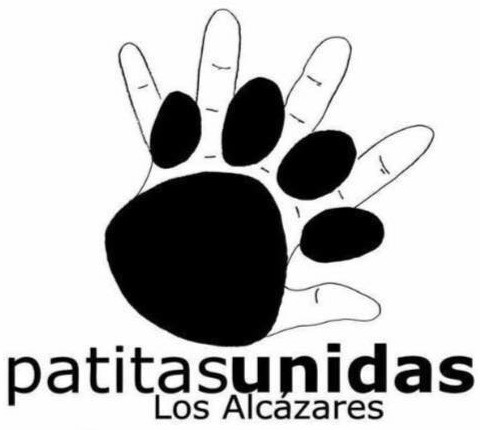
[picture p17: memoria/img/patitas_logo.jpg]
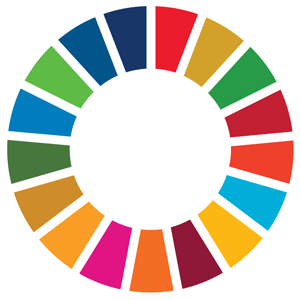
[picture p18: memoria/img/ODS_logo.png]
				 &    \\
				(a)  & (b) \\ [10pt]
			\end{tabular}
			\caption{Logos de la protectora de Patitas Unidas Los Alcázares [\ref{bib: web patitas}] y de los Objetivos de Desarrollo Sostenible (ODS) [\ref{bib: ods}], respectivamente.}
			\label{fig: estado del arte logos}
		\end{center}
	\end{figure}

	\subsection[Resumen del capítulo]{Resumen del capítulo}
	
	\noindent En este capítulo, se ha presentado el contexto actual en el que se presenta este proyecto, cómo se cataloga dentro del ámbito de los Trabajos Fin de Estudios, y qué proyectos similares Open Source existen en la actualidad. Durante la planificación de este proyecto, se realizó una búsqueda de proyectos Open Source, que si bien no realizan la totalidad de funcionalidades que queremos cubrir con este proyecto, de manera individual sí cubrían algunas de las funcionalidades de interés, como son la alimentación autónoma de animales, monitorización de proyectos a través de LoRa y alimentación autónoma de dispositivos. Se han mostrado ejemplos de dichos proyectos.
	
	\pagebreak
	
	\section[Diseño del sistema]{Diseño del sistema}
	\label{Sección 3: Diseño del sistema}
	\noindent A lo largo de este capítulo se pretende mostrar los procesos de concepción, análisis e investigación llevados a cabo para la creación del primer prototipo del sistema de alimentación. Para ello, primeramente, se exponen las funcionalidades que éste debe incorporar; una vez identificadas esas funcionalidades, se presta la realización de una investigación cuyo objetivo sea la búsqueda de opciones que permitan que cada funcionalidad anteriormente expuesta pueda materializarse. Para terminar el presente capítulo, se procederá a exponer las opciones que han sido escogidas, debidamente justificadas, para el diseño del prototipo provisional del sistema de alimentación. 
	
	\subsection[Funcionalidades a cubrir]{Funcionalidades a cubrir}
	\label{subsection: funcionalidades a cubrir}
	
	\noindent Teniendo claros los objetivos que se persiguen con este proyecto, es posible definir las funcionalidades que ofrecería el sistema global que se pretende crear, ya que a partir de esta definición podremos empezar a deducir y establecer qué componentes son necesarios para llevar a cabo dichas funcionalidades. \\
	
	\noindent Definimos \textit{tres funcionalidades principales}: 
	
	\begin{enumerate}
		\item \textbf{Alimentación autónoma del dispositivo}
		\item \textbf{Automatización y monitorización}. Esta funcionalidad se compone de cuatro grandes bloques:
		\begin{itemize}
			\item Bloque microcontrolador
			\item Bloque comunicación radio 
			\item Bloque comedero (sensores, actuadores)
			\item Bloque bebedero (sensores, actuadores)
		\end{itemize}
	
		\item \textbf{Integridad mediante prototipo exterior}. Se entiende por \textit{Integridad mediante prototipo exterior} todos aquellos elementos que usemos para dar forma al proyecto, evitando el uso de elementos demasiado temporales como pueden ser una protoboard o en general, componentes no definitivos (estos sólo se usarán en pruebas, no en producción). Con esta  idea, se buscarán elementos que permitan constituir un primer prototipo usable, sin invertir dinero en exceso, que elimine componentes temporales no funcionales para usar en la ubicación real; es por ello, que se cuenta con la inversión en reservas, conexionado de reserva a comedero/bebedero, diseño de una PCB, etc.
	\end{enumerate}
	
	\subsection[Búsqueda soluciones]{Búsqueda de soluciones para cada funcionalidad}

	\subsubsection{Alimentación autónoma del dispositivo}
	\label{subseccion 3.2.1: búsqueda soluciones alimentación}
	\noindent Se entiende por alimentación autónoma la obtención de energía suficiente para el correcto funcionamiento de un dispositivo o un sistema, y que dicha obtención de energía se realice de manera cíclica e independiente o prácticamente independiente, es decir, no dependa de la acción y supervisión constante de una persona. \\
	
	\noindent Para determinar la forma en la que alimentaremos nuestro proyecto es imprescindible conocer bien las necesidades energéticas que lo limitarán [\ref{bib: adafruit pick the right battery}]; hay que determinar, por tanto, el consumo estimado de los componentes que conforman el proyecto. También es importante saber el tamaño y/o el destino de nuestro proyecto, para determinar si estará limitado a la hora de su transporte por una fuente de alimentación pesada, o si esta no limita en absoluto; será fundamental, además, conocer la ubicación de nuestro proyecto, es decir, si estará en el exterior o interior, si el ambiente será excesivamente frío, cálido o húmedo.\\
	
	\noindent A continuación, se mencionarán algunas soluciones para alimentación autónoma. Primero, se realizará una introducción teórica a términos y definiciones que nos permitan entender su funcionamiento; después, se presentarán opciones dentro de la categoría, haciendo énfasis en sus ventajas y desventajas, y anotando para qué proyectos es recomendable su uso. Por último, se pueden mostrar datos comparativos entre las opciones dentro de la categoría para una mejor visualización de dichas diferencias.\\ 
	
	\noindent \textbf{Baterías recargables} \\
	
	\noindent \textit{Términos y definiciones} \\
	
	\noindent Las características eléctricas de una batería definen cómo actuará en el circuito global, y las características físicas tendrán un enorme impacto en el tamaño y peso global del producto al que va a alimentar. Es por ello que, a la hora de escoger una batería, hay que tener presente los requerimientos de alimentación del proyecto, ya que ésta debe ser capaz de suministrar suficiente energía para que funcione correctamente, sin que sus características físicas supongan una limitación. Algunos parámetros que hay que comprobar son la tensión nominal, la corriente, la capacidad y el material del que está hecha la batería, pero no son los únicos a tener en cuenta. Se presenta, a continuación, una lista más extensa de los parámetros más importantes de las baterías [\ref{bib: TI rechargeable batteries}]: 
	
	\begin{itemize}
		\item  Una \textit{\textbf{celda}} es un dispositivo electroquímico capaz de suministrar la energía que resulta de una reacción química interna a un circuito eléctrico externo. \\
		Una batería se compone de una o más celdas, conectadas en paralelo o en serie para obtener la capacidad de corriente/voltaje requerida (las baterías compuestas por celdas conectadas en serie son las más comunes).
		\item La \textit{\textbf{resistencia en serie equivalente (ESR)}} es la resistencia interna presente en cualquier celda que limita la cantidad de corriente máxima que puede entregar.
		\item La \textit{\textbf{capacidad}}, medida en amperio-hora (Ah), de una batería (o celda) es su figura de mérito más importante: se define como la cantidad de corriente que una batería puede entregar durante 1 hora antes de que el voltaje de la batería llegue al final de su vida útil. 
 		\item La \textit{\textbf{tasa ``c''}}  es una corriente que es numéricamente igual a la clasificación Ah de la celda. Las corrientes de carga y descarga se expresan típicamente en fracciones o múltiplos de la tasa c. 
 		\item El \textit{\textbf{MPV (voltaje de punto medio)}} es el voltaje nominal de la celda y es el voltaje que se mide cuando la batería se ha descargado el 50\% de su energía total. \\
 		\noindent La oscilación de voltaje máxima y mínima del valor nominal es una consideración de diseño importante: una curva de descarga ``más plana" significa menos variación de voltaje que el diseño debe tolerar.
 		\item El \textit{\textbf{voltaje de celda medido al final de su vida útil}} se llama \textit{\textbf{EODV}}, que significa \textit{Fin de voltaje de descarga} (algunos fabricantes se refieren a esto como \textit{EOL} o \textit{voltaje de fin de vida útil}). \\
 		\noindent Cuando se carga al máximo, el voltaje real de la celda será más alto que el MPV. Al acercarse al punto EODV (final del voltaje de descarga), el voltaje de la celda será menor que el MPV (ver Figura \ref{fig: curva carga descarga bateria}). 
 		\item La \textit{\textbf{densidad de energía gravimétrica}} de una batería es una medida de cuánta energía contiene una batería en comparación con su peso. Normalmente viene expresada en Watt-horas/kilogramo (Wh/kg).
 		\item La \textit{\textbf{densidad de energía volumétrica}} de una batería es una medida de cuánta energía contiene una batería en comparación con su volumen. Normalmente se expresa en Watt-horas/litro (Wh/l)
 		\item Un \textit{\textbf{cargador de voltaje constante}} es un circuito que recarga una batería obteniendo solo la corriente suficiente para forzar el voltaje de la batería a un valor fijo.
 		\item Un \textit{\textbf{cargador de corriente constante}} es un circuito que carga una batería al suministrar una corriente fija a la batería, independientemente del voltaje de la batería.
	\end{itemize}

	%\pagebreak
	
	\begin{figure}[h!]
		\begin{center}
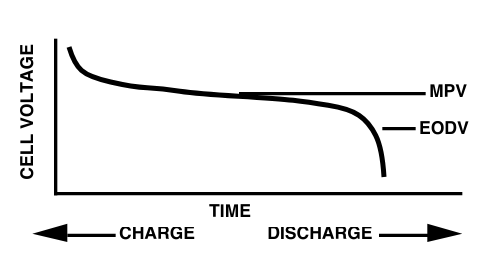
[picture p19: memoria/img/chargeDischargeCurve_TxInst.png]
			
			\caption{Curva de la carga/descarga de una batería [\ref{bib: TI rechargeable batteries}].}
			\label{fig: curva carga descarga bateria}
		\end{center}
	\end{figure}

	\pagebreak

	% \noindent Entrarían dentro de esta categoría  las conocidas baterías recargables, formato LiPo o Li-ion, por ejemplo, o formato powerbank, que si bien en su interior usan baterías LiPo/Li-ion, el encapsulado en el que se presentan y la forma en que se usan son totalmente diferentes. \\
	
	\noindent \textit{Tipos de baterías recargables}\\
	
	\noindent Las principales baterías recargables [\ref{bib: Hackaday battery basics}][\ref{bib: YouTube How to choose  a battery}][\ref{bib: blog diferencias li-ion y li-po}] que existen son: 
	
	\begin{enumerate}
		
		\item \textit{Lithium polymer} (LiPo).  Son baterías de gran densidad de energía disponible, es decir, almacenan una gran cantidad de energía en comparación con el tamaño de la pila (se explica en \textit{Términos y definiciones}). Es por esta razón por la que los teléfonos móviles, los portátiles y otros dispositivos ligeros en peso usan baterías LiPo. Sin embargo, esta alta densidad de energía lleva consigo un coste/inconveniente, y es que son caras, y no son sólo las baterías en sí; cuando se trabaja con baterías de litio, hay que realizar una inversión para conseguir una circuitería especial que mantenga segura la batería. Por ejemplo, cuando estas cargando una batería LiPo, hay que asegurarse de que nunca se excedan los 4.2V por celda; las baterías LiPo explotarían si las sobrecargaras. No solo la carga de la batería es delicada, sino que la descarga también lo es; si se descarga una batería LiPo por debajo de 3V por celda, se perderá permanentemente parte de su capacidad, e incluso pueden deformarse/hincharse. Finalmente, hay que estar pendiente constantemente de la temperatura, para evitar que la batería se sobrecaliente. A pesar de todo esto, es común usar baterías LiPo en proyectos ligeros y pequeños, siempre y cuando se tenga un buen circuito de carga, un buen circuito de descarga (que proteja a valores bajos de tensión, haciendo de corte en el mínimo de tensión de la batería) y un buen circuito de monitorización de temperatura. 
		
		\item \textit{Lithium-ion} (Li-ion). Son muy similares a las baterías LiPo, pero a diferencia de estas, el electrodo negativo es líquido y el encapsulado y formato de presentación es totalmente diferente (las Li-ion suelen venderse sin protección y en apariencia son similares a unas pilas alcalinas AA). Una batería Li-ion almacena más potencia que las LiPo (mayor capacidad), ofrece mayores corrientes de descarga, es menos costosa de fabricar (y por tanto tienen un precio de venta más asequible),  y tiene un tiempo de vida más largo (aunque con el tiempo pierde sus propiedades). Es, al igual que las LiPo, inflamable si se daña, se calienta en exceso o se sobrecarga. El empaquetado más común es el 18650, y en el mercado existen circuitos de protección varios para evitar la sobrecarga y la sobredescarga  para este encapsulado en concreto, por lo que es una opción barata y sencilla para conseguir un prototipado rápido y realizar pruebas del mismo, siempre y cuando el proyecto no exija mucha potencia; si el proyecto exigiera más tensión de la que proporciona la batería, se puede considerar obtener más unidades y realizar una configuración en serie para aumentar la tensión, o en paralelo si lo que se desea es aumentar la capacidad, o una combinación de ambas configuraciones (usando siempre un \textit{Battery Management System} o BMS, para mantener las baterías balanceadas entre sí). Esta opción se puede considerar para baterías LiPo, pero para usuarios principiantes o poco experimentados resultará, probablemente, más complejo.
		
		\item \textit{Lithium Iron Phosphate} (LiFePO4). Son similares a las baterías LiPo, con la salvedad de que no son propensas a explosiones, como lo pueden ser las LiPo, si no se manipulan correctamente o las condiciones anteriormente mencionadas no se dan. También requieren una apropiada circuitería para cargarlas y descargarlas con cuidado, y si se comete un error se perderá permanentemente parte de la capacidad de la batería. Además, son un poco más pesadas que las baterías LiPo. Se usan normalmente en robots ligeros, herramientas eléctricas y juguetes por radio control, ya que son baterías bastante buenas entregando grandes cantidades de energía en un formato pequeño y liviano.
		
		\item \textit{Sealed lead-acid} (SLA). Son una opción si se quiere comprar una batería no muy costosa, a la vez de evitar enfrentarnos a circuitos de protección de la batería. Estas baterías son bastante más duraderas que una batería de litio, y también son mejores para hacer frente a sobrecargas accidentales o sobredescargas. Tienen una excelente relación calidad-precio y también son el mejor tipo de batería frente a temperaturas extremas; es por esta razón que las baterías de plomo (o ácido-plomo) son la opción estándar para coches, motos, almacenamiento de energía solar y fuentes de alimentación de emergencia. El inconveniente de usar baterías de plomo es que son grandes y pesadas. No es recomendable, por tanto, usar baterías de plomo en aplicaciones portátiles.
		
		\item Níquel-cadmio (\textit{Nickel-cadmium}, NiCd). Los dispositivos portátiles, como los primeros teléfonos móviles, usaban baterías de níquel-cadmio. Son baterías baratas, que en teoría duran más tiempo que las baterías SLA; sin embargo, sufren el llamado efecto memoria, por lo que hay que regularmente descargarlas por completo, luego recargarlas por completo para mantener una alta capacidad, ya que, de lo contrario, estaríamos perdiendo vida útil de la batería. Así pues, en la actualidad no se suele usar este tipo de baterías, aunque se siguen vendiendo.
		
		\item \textit{Nickel Metal Hydride} (NiMH). Las baterías de níquel-metalhidruro o de níquel hidruro metálico tienen una mayor densidad de energía que las baterías de níquel-cadmio, en tanto a precio no son mucho más costosas y no sufren el efecto memoria. Son más grandes y pesadas que las baterías de litio, pero es bastante seguro trabajar con ellas, por lo que son las baterías más usadas por el consumidor medio en términos de pilas recargables (las encontramos en cualquier supermercado, y cargarlas es barato y simple). Hay que tener en cuenta que las baterías de NiMH, por norma general, tienen un ratio de autodescarga elevado, lo que quiere decir que a pesar de que no se esté haciendo uso de la batería, se autodescargan igualmente en un par de meses, lo que hace que no sean una buena opción para objetos de uso cotidiano (como mandos a distancia). Se recomienda que, si se necesita hacer uso de este tipo de baterías, se adquieran con bajo ratio de autodescarga (como Panasonic Eneloop), las cuales pueden resultar más baratas a largo plazo que comprar unas pilas alcalinas.
		
	\end{enumerate}
	
	\noindent \textit{Comparativa entre tipos de baterías recargables} \\
	
	\noindent Hemos visto que existen diferentes tipos de baterías, las cuales podemos comparar entre ellas basándonos en diferentes parámetros. Fijándonos de nuevo en un estudio de \textit{Texas Instruments} [\ref{bib: TI rechargeable batteries}], el cual compara baterías de Ni-MH, Ni-Cd y Li-Ion, algunos parámetros que podemos comparar son:
	
	\begin{itemize}
		\item \textit{\textbf{Densidad de energía}}. La batería Li-Ion duplica en densidad gravimétrica a las baterías Ni-MH y Ni-Cd, lo que significa que el producto que emplee una batería Li-Ion será más liviano y durará más tiempo la propia batería
		
		\item \textit{\textbf{Estabilidad de tensión o tensión de celda}}. 	La tensión proporcionada para alimentar la carga es la más importante: las baterías Ni-Cd y Ni-MH tienen una tensión por celda de 1.25V (sus tensiones de descarga se asumen por norma general idénticas). \\
		La tensión por celda de las baterías Ni-Cd y Ni-MH son sólo una tercera parte de la tensión nominal de 3.6V proporcionada por una celda de Li-ion Lo que significa que se requerirían tres celdas de Ni-Cd/Ni-MH conectadas en serie para igualar la tensión de una única celda de Li-ion.\\
		Sin embargo,su curva de descarga es extremadamente plana, próxima a la de una batería ideal. Esta importante diferencia entre tipos de baterías significa que las celdas de Ni-Cd y Ni-MH son adecuadas para su uso con reguladores lineales, pero las baterías de Li-ion requieren convertidores reductores (\textit{buck converters}) para obtener una buena eficiencia de conversión de energía en la fuente de alimentación. 
		
		\item \textit{\textbf{Corriente pico}}, \textit{\textbf{Autodescarga}}, etc. No entraremos en más detalle por no extender en exceso la longitud del documento, pero si es de interés, se puede consultar la fuente, ya incluida en el apartado bibliográfico.
	\end{itemize}

	\noindent \textbf{Panel solar}\\ 
	
	\noindent Un panel solar, por si solo, no realiza la tarea de alimentación autónoma. Requiere, como mínimo, de una batería donde almacenar la energía que captan, por lo que, necesariamente, habría que escoger entre algunas de las opciones planteadas en el apartado anterior. Además, una batería no irá conectada directamente al panel solar, ya que se requiere un cargador solar que haga de intermediario, por una parte, entre la batería y el panel, y por otra parte, entre la batería y el dispositivo al que alimenta dicha batería. \\
	
	\noindent Aunque esto será explicado con más detalle más adelante, se considera necesario establecer desde un principio los requerimientos mínimos para poder usar un panel solar de cara a la funcionalidad de alimentación autónoma, ya que dependen del apartado que acabamos de presentar sobre baterías recargables, y estos requerimientos mínimos establecerán una base de cara a la explicación sobre sistemas fotovoltaicos más complejos. \\
	
	\noindent \textit{Funcionamiento y composición de un panel solar}\\

	%\pagebreak
	
	\noindent Un panel solar es una agrupación de muchas células fotovoltaicas (PV) que están cubiertas con vidrio protector y unidas con un marco de metal (ver Figura \ref{fig: capas panel solar}). Es por eso que el nombre oficial de un panel solar es ``módulo fotovoltaico" (\textit{PV module}). Estas células solares fotovoltaicas están hechas de material semiconductor, generalmente silicio, que se corta en tiras muy finas.\\
	
	\noindent Los paneles solares tienen muchas capas. La capa de células fotovoltaicas es donde se produce la electricidad. Otras capas, como las capas de vidrio y encapsulante, están ahí para proteger las células fotovoltaicas para que los módulos puedan producir electricidad de manera adecuada.\\
	
	\pagebreak
	
	\begin{figure}[h!]
		\begin{center}
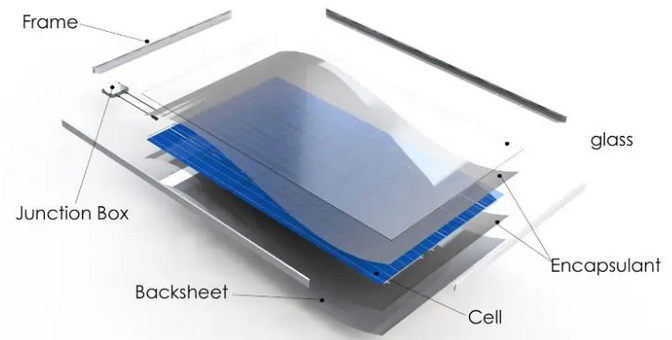
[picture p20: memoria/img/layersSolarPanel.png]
			
			\caption{Capas y componentes que componen un panel solar [\ref{bib: solar reviews how solar panels work}].}
			\label{fig: capas panel solar}
		\end{center}
	\end{figure}

	\noindent Cada célula fotovoltaica tiene una capa negativa y una capa positiva. Para que un panel solar genere electricidad solo necesitamos algo de energía para hacer que esos electrones fluyan de la capa negativa a la capa positiva. \\
	
	\noindent Así pues, en resumen, la energía de los fotones del sol hace que los electrones en el lado negativo de la celda fotovoltaica se muevan (existe electricidad). Esto se llama \textit{efecto fotovoltaico} (ver Figura \ref{fig: efecto fotovoltaico}).\\
	
	\begin{figure}[h]
		\begin{center}
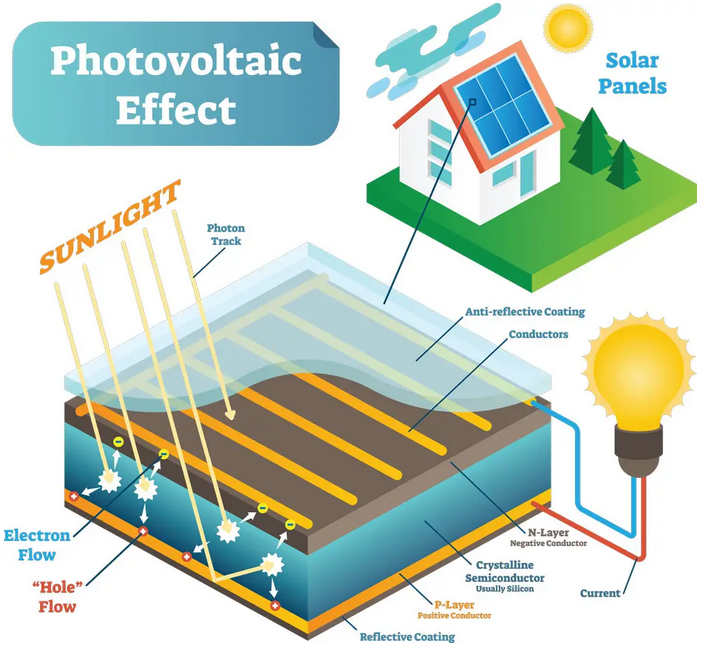
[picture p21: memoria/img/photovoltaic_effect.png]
			
			\caption{Dibujo representativo del efecto fotovoltaico [\ref{bib: solar reviews how solar panels work}].}
			\label{fig: efecto fotovoltaico}
		\end{center}
	\end{figure}
	
	\pagebreak
	
	\noindent Los electrones necesitan un camino a seguir y la electricidad debe estar en una forma útil. Es por ello que la ruta que creemos para los electrones (el circuito) es importante, ya que, cuando salen de la capa negativa de la celda fotovoltaica, queremos que fluyan a través de nuestras cargas (como nuestras luces y electrodomésticos, en el ejemplo del uso doméstico) para que los electrones puedan dar energía a esas cargas a medida que avanzan hacia la capa positiva de la celda fotovoltaica. \\
	
	%\noindent \textit{¿explicación sistema fotovoltaico?} \\
	
	\noindent Un elemento muy importante en este sentido es el inversor, el cual convierte la energía DC producida por un panel solar, a energía AC, lista para ser usada en el hogar. Sin embargo, para nuestro proyecto no es necesario, ya que nos interesa crear un proyecto que se alimente de manera autónoma, sin uso de la electricidad disponible en el hogar; el panel solar, en este caso, recargaría una pila, y por ello necesitamos la energía DC, y no necesitamos usar un inversor a AC. \\ 
	
	\noindent \textit{Parámetros}\\
	
	\noindent Los principales paramétros [\ref{bib: TU delft OCW solar cell param}] que se usan para caracterizar el rendimiento de las células solares son la potencia máxima $P_{max}$ (\textit{peak power}), la densidad de corriente en cortocircuito $J_{sc}$, la tensión en circuito abierto $V_{oc}$, y el factor de forma \textit{FF}. Estos parámetros se determinan a partir de la curva J-V característica cuando la célula está iluminada, tal como se muestra en la Figura \ref{fig: curva J-V célula solar} (existe también la curva I-V, como la de la Figura \ref{bib: research gate pv cell param}). La eficiencia de conversión $\eta$ se puede determinar a partir de estos parámetros. \\
	
	\noindent Nótese que se menciona específicamente \textit{parámetros de una célula solar}; un panel solar, como se ha mencionado anteriormente, consta de varias células fotovoltaicas, por lo que los parámetros especificados, en términos globales y tal como se construyen los paneles solares, influyen en las especificaciones finales del panel según el número de células del que conste (ver Figura \ref{fig: solar panel of identical solar cells}). \\
		\begin{figure}[h]
		\begin{subfigure}{0.5\textwidth}
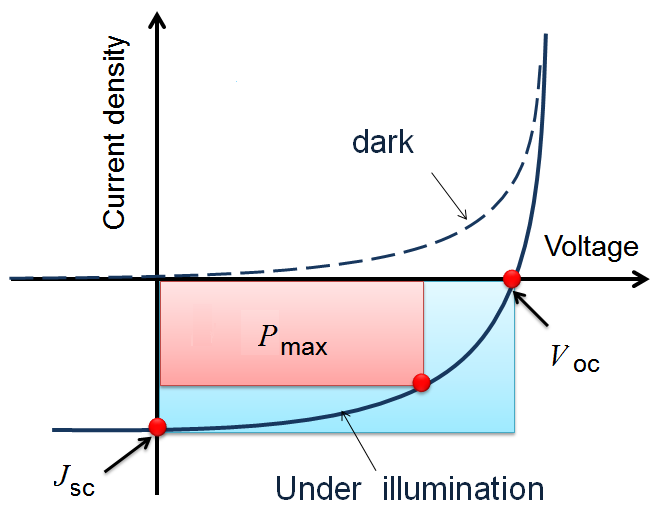
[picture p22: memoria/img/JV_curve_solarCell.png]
			 
			\caption{Determinación de los parámetros de una célula solar a partir de su curva J-V [\ref{bib: research gate JV curve solar panel}].}
			\label{fig: curva J-V célula solar}
		\end{subfigure}
		\begin{subfigure}{0.5\textwidth}
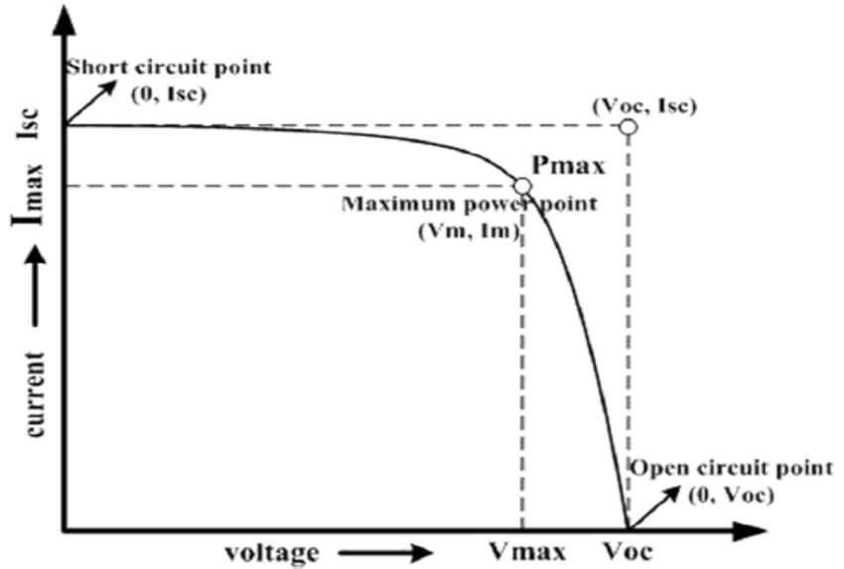
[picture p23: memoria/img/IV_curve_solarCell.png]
			
			\caption{Curva I-V de una célula solar [\ref{bib: research gate pv cell param}].}
			\label{fig: I-V curve of a solar cell}
		\end{subfigure}
		\caption{Curvas J-V e I-V de una célula fotovoltaica [\ref{bib: research gate JV curve solar panel}][\ref{bib: research gate pv cell param}]}
		\label{fig:curvas J-V e I-V célula PV}
	\end{figure}

	\begin{figure}[h]
		\begin{center}
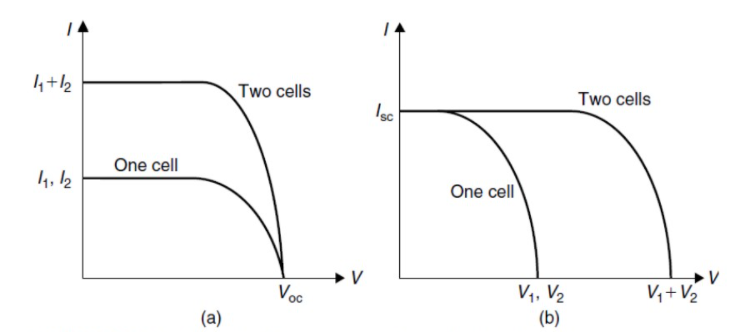
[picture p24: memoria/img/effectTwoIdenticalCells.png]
			
			\caption{Comportamiento de un panel solar formado por dos células solares idénticas [\ref{bib: SlidePlayer Photovoltaic systems}].}
			\label{fig: solar panel of identical solar cells}
		\end{center}
	\end{figure}

	\noindent Para realizar medidas fiables y definir la curva característica J-V, se deben realizar las medidas bajo condiciones estándar de pruebas (\textit{standard test conditions, STC}); estas son, una temperatura constante a $25^{\circ}C$, una irradiancia total de 1000 $W/ m^2$ y un espectro solar de AM1.5 (sol directo y con ángulo cenital de $48,2 ^{\circ}$). Esto lo tendremos en cuenta si queremos comprobar que las especificaciones del producto son correctas, o por el contrario el producto viene tiene defectos. En este proyecto no es prioritario el estudio profundo y comprobación exhaustiva del panel solar, por lo que no se realizarán dichas pruebas; sin embargo, sí realizaremos un estudio teórico de los parámetros que definen a una célula solar, como también lo hemos hecho de los materiales que lo componen y su funcionamiento general.\\

	\noindent \textit{\textbf{Densidad de corriente en cortocircuito}} \\
	
	\noindent La corriente en cortocircuito $I_{sc}$ es la corriente que fluye a través de un circuito externo cuando los electrodos de una célula solar se cortocircuitan. La corriente en cortocircuito de una célula solar depende de la incidencia del flujo de fotones sobre ella, la cual está determinada por el espectro de la luz incidente. También depende del área de la célula solar. Para eliminar la dependencia del área de la célula solar sobre $I_{sc}$, normalmente se usa la densidad de corriente en cortocircuito para describir la máxima corriente entregada por una célula solar. La máxima corriente que una célula solar puede entregar depende mucho de las propiedades ópticas de la célula solar, tales como la absorción en la capa absorbente y la reflexión. \\
	
	\noindent Las células solares de silicio cristalino pueden entregar, bajo un espectro AM1.5, una posible densidad de corriente máxima de 46 $mA/cm^2$. En las células solares de c-Si de laboratorio, las medidas de $J_{sc}$ están por encima de 42 $mA/cm^2$, mientras que las células solares comerciales tienen un $J_{sc}$ que excede los 35 $mA/cm^2$. \\
	
	\noindent \textit{\textbf{Tensión en circuito abierto, $V_{oc}$}} \\
	
	\noindent Es la tensión máxima que una célula solar puede entregar. $V_{oc}$ corresponde a la tensión de polarización directa, a la cual la densidad de corriente de oscuridad compensa la densidad de corriente fotovoltaica (\textit{fotocorriente}). Depende de la densidad de corriente de saturación de la célula solar y de la corriente fotogenerada. Mientras ésta última varía poco, la corriente de saturación puede variar en órdenes de magnitud. La corriente de saturación depende de la recombinación en la célula solar, por lo que $V_{oc}$ es una medida de la cantidad de recombinación de la célula solar.\\
	
	\noindent Las células solares de laboratorio hechas de silicio cristalino dan valores de $V_{oc}$ de hasta 720 mV bajo condiciones AM1.5 estándar, mientras que las células solares comerciales normalmente dan valores de $V_{oc}$ por encima de los 600 mV. \\
	
	\pagebreak
	
	\noindent \textit{\textbf{Factor de forma}} \\
	
	\noindent El factor de forma es la relación entre la potencia máxima ($P_{max} = J_{mpp} V_{mpp}$) generada por una célula solar y el producto de $V_{oc}$ con $J_{sc}$. \\
	
	\noindent El subíndice \textit{mpp} hace referencia al \textit{punto de potencia máxima} (\textit{maximum power point, MPP}) de la célula solar, es decir, el punto de la curva característica J-V de la célula solar al cual la célula solar ofrece su máxima potencia de salida.  Para optimizar la operación de los sistemas fotovoltaicos, es muy importante que las células solares (o módulos fotovoltaicos) operen sobre el MPP. Esto se puede asegurar con un seguidor de punto de máxima potencia (\textit{maximum power point tracking, MPPT}[\ref{bib: energia solar regulador de carga}][\ref{bib: CED greentech how mppt works}]). Se trata de un algoritmo, el cual se usa en controladores de carga solar para extraer la máxima potencia disponible del módulo fotovoltaico bajo ciertas condiciones; dichas condiciones (se entrará más en detalle más adelante), como son la radiación solar a lo largo del día y año, la temperatura ambiente y la temperatura de la célula, afectan a la potencia máxima de salida de la misma, y es entonces cuando un MPPT actúa, haciendo operar a la célula solar al valor de tensión más eficiente, el MPP. El controlador de carga mantiene la tensión y la corriente a un nivel optimizado, donde el módulo fotovoltaico brinda la mayor cantidad de energía a la carga; es ``consciente'' del estado de carga de la batería y actúa en consecuencia. \\
	
	\noindent El uso de un seguidor de punto de máxima potencia, sin embargo, encarece el costo total de un proyecto; si bien para aplicaciones que requieran la extracción de la máxima potencia de un panel solar (por limitaciones de espacio, por ejemplo, donde deberíamos explotar las características de los paneles que pudiéramos colocar), en el proyecto que estamos diseñando no es el caso, por lo que no usaremos herramientas de este estilo. Además, aunque pueden encontrarse o construirse de manera aislada (se trata de un conversor DC a DC), también suelen encontrarse incorporados a inversores, los cuales tampoco son necesarios, ya que no es energía solar para uso en hogar. Como anotación, existen otros controladores de carga que no son MPPT, como el PWM o \textit{shunt controller} (regulador de carga tipo paralelo o de desviación). \\
	
	\begin{figure}[h]
		\begin{center}
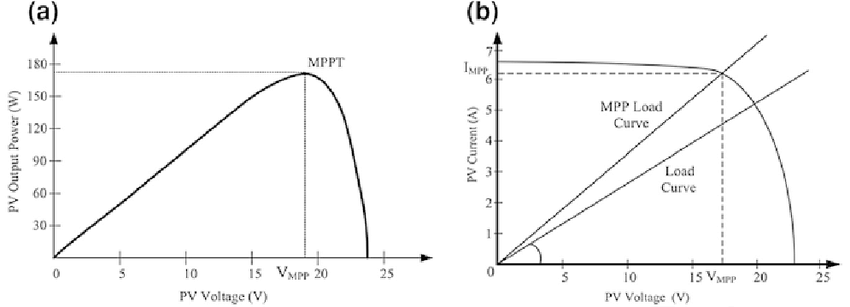
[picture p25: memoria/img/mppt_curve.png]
			
			\caption{Curva P-V de una célula solar, indicando el punto MPP [\ref{bib: research gate mppt curve}].}
			\label{fig: MPPT in P-V curve of a solar cell}
		\end{center}
	\end{figure}
	
	\noindent Por último, anotar que el factor de forma no varía tanto con $V_{oc}$, sino más con el material del que están hechas las células solares. \\
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

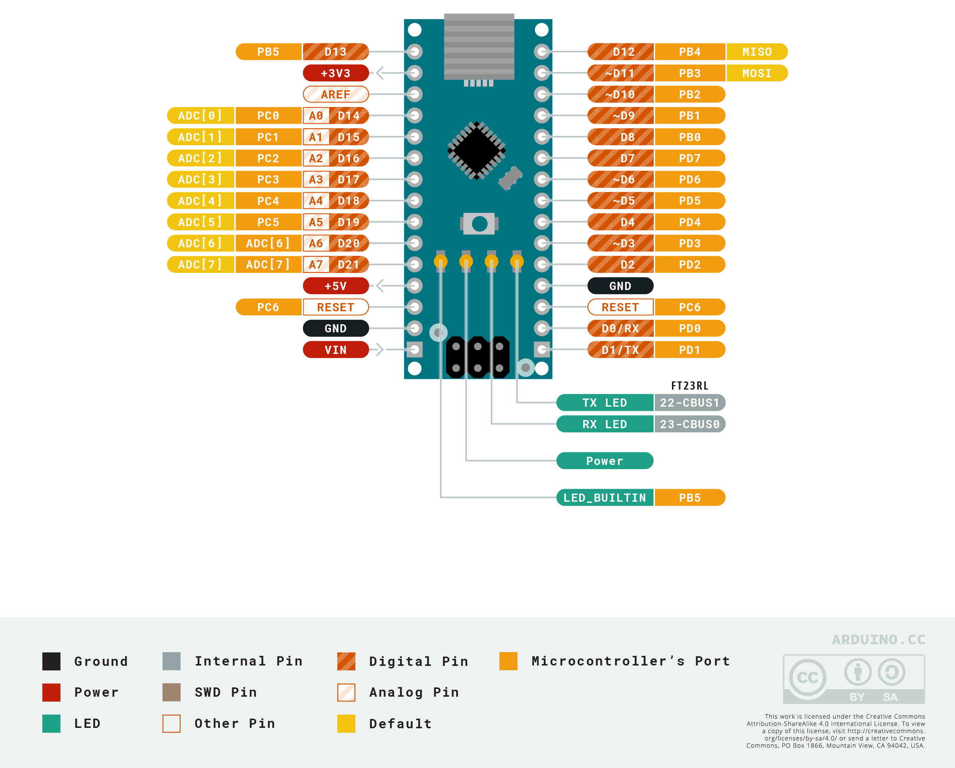
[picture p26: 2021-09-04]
memoria/img/Pinout-NANO_official.png

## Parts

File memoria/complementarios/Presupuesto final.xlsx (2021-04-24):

Producto |  | Sección | Precio ud | Cantidad | Envío | Total | En el prototipo provisional | En el prototipo final
Cuenco acero inoxidable |  | Prototipo exterior | 4.29 | 2 | 0 | 8.41 | Sí
Caja eléctrica de cable (grande) |  | Prototipo exterior | 4.75 | 1 | NA | 4.75 | Sí
Caja eléctrica de cable (pequeña) |  | Prototipo exterior | 3.95 | 1 | NA | 3.95 | Sin determinar |  | Tipos de secciones
Bobina de cable |  | Prototipo | 12.01 | 1 | 0 | 12.01 | Sí |  | Prototipo exterior: lo que conforma el sistema por fuera y que nos ayudará a probar el funcionamiento del sistema global
Tubo silicona |  | Bebedero | 1 | 2m | NA | 1 | Sí |  | Bebedero: lo usado para el movimiento del agua desde la reserva hasta el bebedero
Pieza PVC en "T" |  | Comedero | 1 | 1 | NA | 1 | Sí |  | Comedero: lo usado para el movimiento del pienso desde la reserva hasta el comedero
Botella multiusos (reserva de pienso) |  | Prototipo exterior | 5.5 | 1 | NA | 5.5 | Sí |  | Radio: lo que concierne al bloque LoRa
Sensor de nivel de agua (switch) |  | Bebedero | 0.56 | 2 | 1.17 | 2.88 | Sí |  | Microcontrolador: lo relacionado con nuestro arduino nano, que será nuestro microcontrolador
Bomba de agua |  | Bebedero | 0.74 | 1 | 1.07 | 1.81 | Sí |  | PCB: conectores que serán necesarios en la placa para anexionar periféricos
TTGO LoRa32 868MHz SX1276 ESP32 (set de 2) |  | Radio | 22,42/set | 1 | 3.94 | 26.35 | Sí |  | Prototipo: conexionado e integridad de la señal en la electrónica del dispositivo, tanto en versión provisional como definitiva
E32-868T30D |  | Radio | 7.5 | 2 | 1.76 | 16.75 | Sí
Antena 868MHz (set de 2) para SDR |  | Radio | 3,89/set | 1 | 0 | 3.89 | Sin determinar
Antena 868MHz (set de 2) para Tx y Rx |  | Radio | 3,76/set | 1 | 3.95 | 7.71 | Sí
Módulo TP4056 |  | Alimentación dispositivo | 0.24 | 2 |  | 0.48 | Sin determinar
OLED 0.96 pulgadas |  | Prototipo exterior | 1.45 | 1 |  | 1.45 | Sí
Arduino nano con cable mini usb |  | Microcontrolador | 2.09 | 2 |  | 4.18 | Sí
 |  |  |  |  | 3.01 | 9.12
Servomotor MG996R |  | Comedero | 2.35 | 1 | 2.73 | 5.08 | Sí
Panel solar 6V 210mA (pack) |  | Alimentación del dispositivo | 5.25 | 1 | 3.04 | 8.29 | Sin determinar
Kit arduino |  | Microcontrolador | 17.43 | 1 | 0 | 17.43 | Sí
Pila recargable Samsung 18650 2600mAh |  | Alimentación del dispositivo | 7.99 | 1 | 0 | 7.99 | Sí
Level shifter 4 canales 3,3V a 5V (set de 10) |  | Radio | 1,37/set | 1 | 1.53 | 2.9 | Sí
Conectores XT30 (set de 10) |  | Alimentación del dispositivo/PCB | 2,25/set | 1 | 0 | 2.25 | Sí
Conectores JST (set de 20) |  | PCB | 1,70/set | 1 | 0.79 | 2.49 | Sí
Adaptador jack a cable (set de 5) |  | Alimentación del dispositivo | 1,23/set | 1 | 0 | 1.23 | Sí
Extensor SMA |  | Radio | 0.6 | 2 | 1.52 | 2.73 | Sí
Surtido resistencias |  | Prototipo | 1,38/set | 1 |  | 1.38 | Sí
Relé 2 vías |  | Bebedero | 1.06 | 1 |  | 1.06 | No
Surtido diodos |  | Prototipo | 1,27/set | 1 |  | 1.27 | Sí
Kit conectores XH2P |  | PCB | 2,57/set | 1 |  | 2.57 | Sí
Alimentador protoboard |  | Alimentación del dispositivo | 0.73 | 2 |  | 1.46 | Sí | No
 |  |  |  |  | 4.46 | 12.2
Step-up converter 3,3V a 5V |  | Alimentación del dispositivo | 0.55 | 2 |  | 1.1 | Sin determinar
Level shifter 8 canales 3,3 a 5V |  | Radio | 0.38 | 2 |  | 0.76 | Sí
Holder batería 18650 |  | Alimentación del dispositivo | 0.5 | 1 |  | 0.5 | Sí
Conversor de 3,3 a 5V |  | Radio | 0.35 | 2 |  | 0.7 | Sin determinar
Módulo TP4056 con regulador |  | Alimentación del dispositivo | 0.42 | 2 |  | 0.84 | Sin determinar
 |  |  |  |  | 2.99 | 6.89
Transistor PN2222A (set 20) |  | Bebedero | 1.49 | 1 | 0 | 1.49 | Sí
Relé 5V (SDR-05VDC-SL-C) |  | Bebedero | 3.08 | 1 | 0 | 3.08 | Sí
Transformador 220VAC a 9VDC (jack) |  | Alimentación del dispositivo | 3.9 | 2 | 0 | 7.8 | Sí
 | Nota: si la suma total de algunos artículos no corresponde con la suma de los precios unidad es porque de manera excepcional se me aplicó un descuento al pagar.
 | NA: No Aplica (comprado en tienda física).
 | Sin determinar: en el momento actual no se ha usado pero se cree que conforme evolucione el desarrollo será usado.

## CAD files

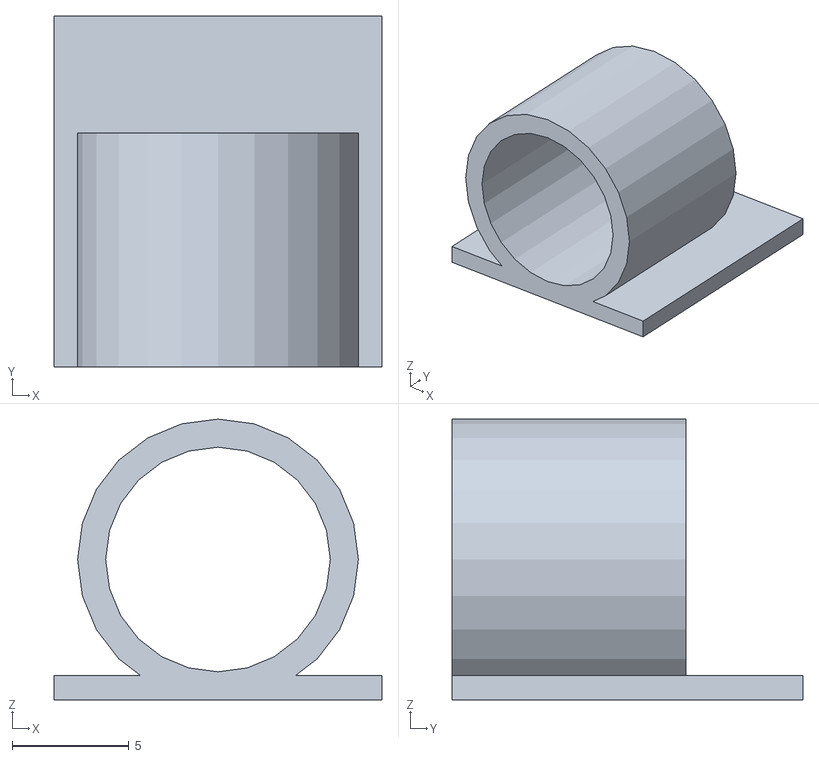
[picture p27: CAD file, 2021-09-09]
hardware/Pieza sujeción bebedero.stl
14.0 x 15.0 x 12.0

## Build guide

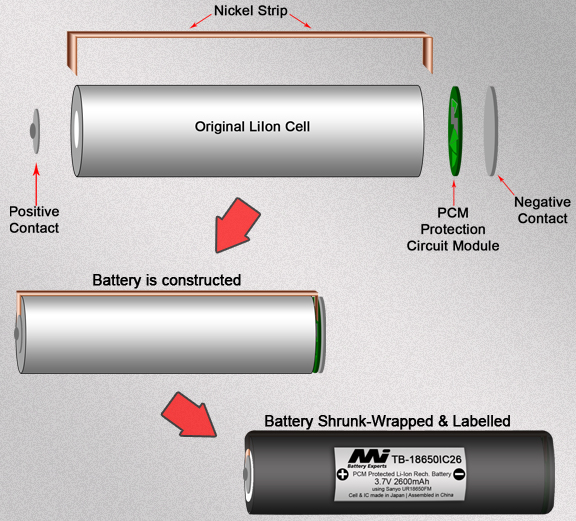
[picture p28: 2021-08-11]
memoria/img/construction_prot_circuit.png

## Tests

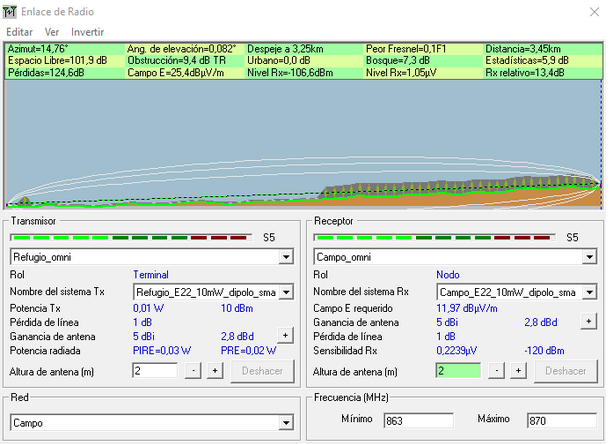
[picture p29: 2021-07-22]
memoria/img/resultado_e22_10mW_conPerdidas_asc.png

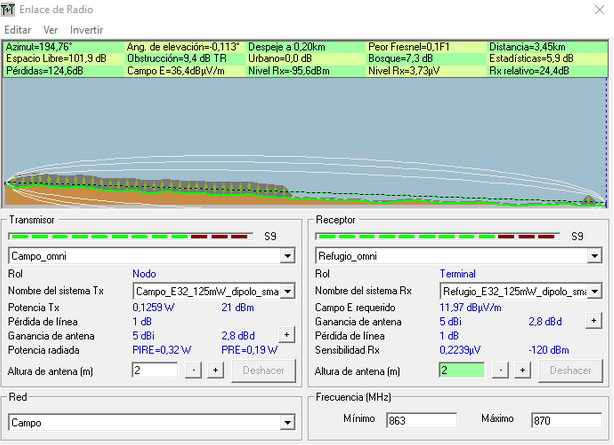
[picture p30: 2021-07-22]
memoria/img/resultado_e32_125mW_conPerdidas_desc.png

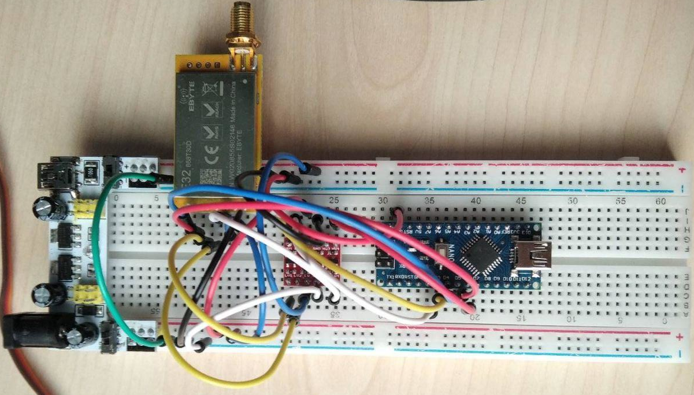
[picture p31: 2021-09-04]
memoria/img/prueba_lora_protoboard_rotated.png

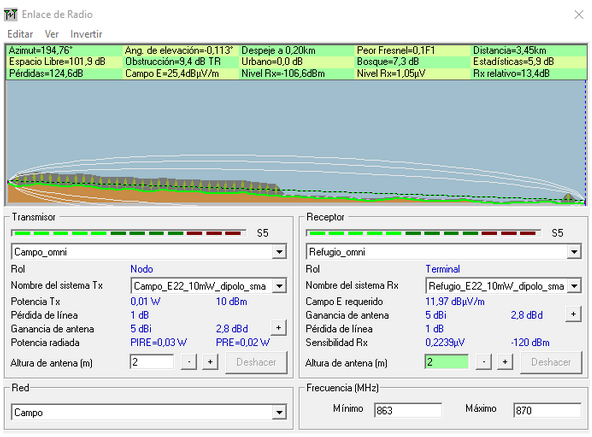
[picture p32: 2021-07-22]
memoria/img/resultado_e22_10mW_conPerdidas_desc.png

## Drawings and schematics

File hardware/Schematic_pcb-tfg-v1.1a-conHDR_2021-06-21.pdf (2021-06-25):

## Arduino Peripherals

## Microcontroller: Arduino nano

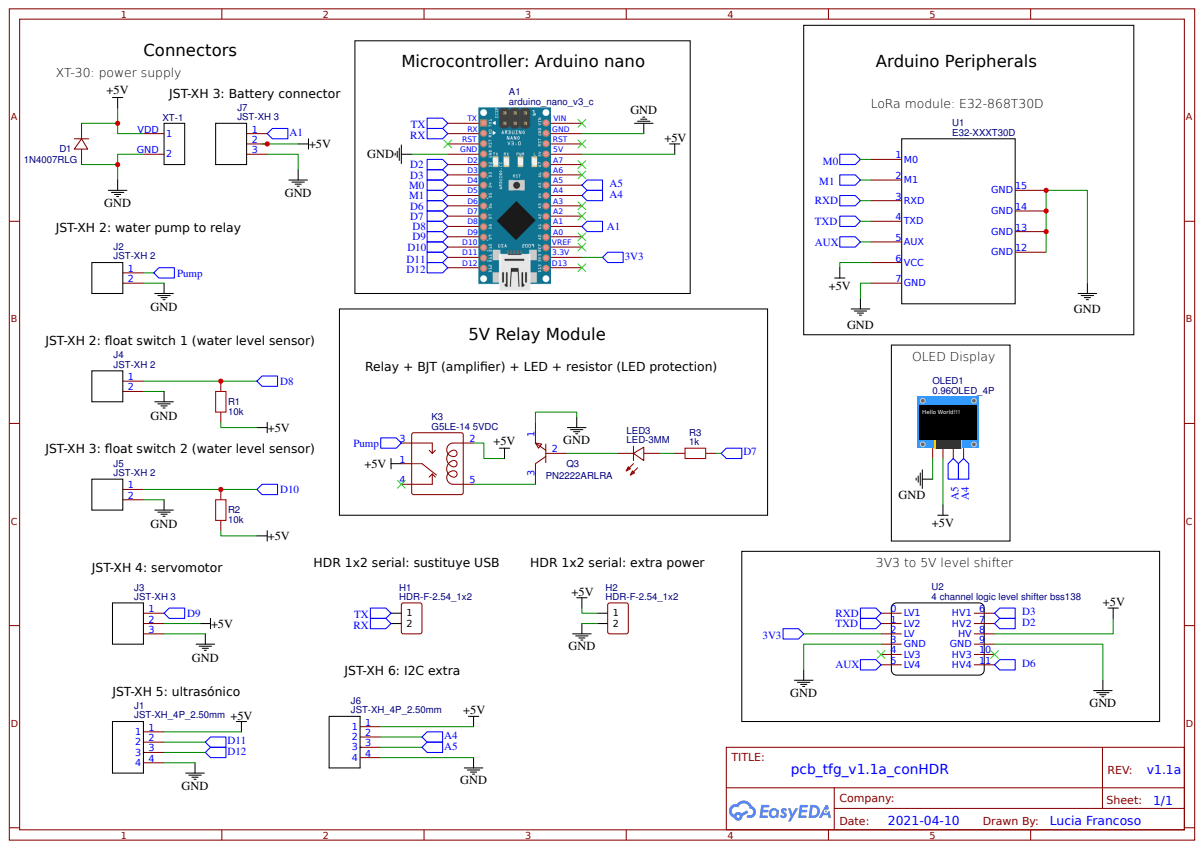
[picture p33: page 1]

JST-XH 3: Battery connector

JST-XH 2: water pump to relay

JST-XH 2: float switch 1 (water level sensor)

Relay + BJT (amplifier) + LED + resistor (LED protection)

JST-XH 3: float switch 2 (water level sensor)

Drawn By: Lucia Francoso

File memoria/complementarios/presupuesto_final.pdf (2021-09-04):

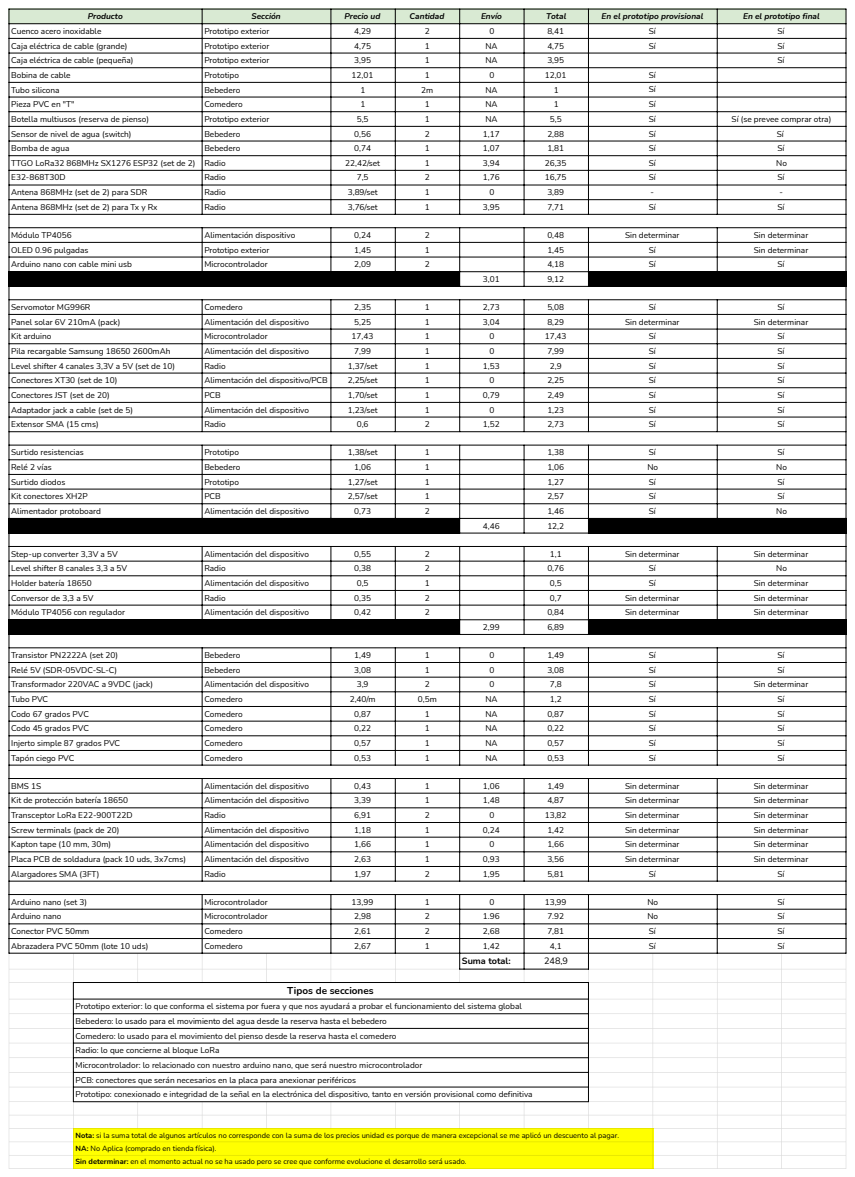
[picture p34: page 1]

Producto | Sección | Precio ud | Cantidad | Envío | Total | En el prototipo provisional | En el prototipo final

Cuenco acero inoxidable | Prototipo exterior | 4,29 | 2 | 0 | 8,41 | Sí | Sí
Caja eléctrica de cable (grande) | Prototipo exterior | 4,75 | 1 | NA | 4,75 | Sí | Sí
Caja eléctrica de cable (pequeña) | Prototipo exterior | 3,95 | 1 | NA | 3,95 | | Sí
Bobina de cable | Prototipo | 12,01 | 1 | 0 | 12,01 | Sí
Tubo silicona | Bebedero | 1 | 2m | NA | 1 | Sí
Pieza PVC en "T" | Comedero | 1 | 1 | NA | 1 | Sí
Botella multiusos (reserva de pienso) | Prototipo exterior | 5,5 | 1 | NA | 5,5 | Sí | Sí (se prevee comprar otra)
Sensor de nivel de agua (switch) | Bebedero | 0,56 | 2 | 1,17 | 2,88 | Sí | Sí
Bomba de agua | Bebedero | 0,74 | 1 | 1,07 | 1,81 | Sí | Sí
TTGO LoRa32 868MHz SX1276 ESP32 (set de 2) | Radio | 22,42/set | 1 | 3,94 | 26,35 | Sí | No
E32-868T30D | Radio | 7,5 | 2 | 1,76 | 16,75 | Sí | Sí
Antena 868MHz (set de 2) para SDR | Radio | 3,89/set | 1 | 0 | 3,89 | - | -
Antena 868MHz (set de 2) para Tx y Rx | Radio | 3,76/set | 1 | 3,95 | 7,71 | Sí | Sí

Módulo TP4056 | Alimentación dispositivo | 0,24 | 2 | | 0,48 | Sin determinar | Sin determinar
OLED 0.96 pulgadas | Prototipo exterior | 1,45 | 1 | | 1,45 | Sí | Sin determinar
Arduino nano con cable mini usb | Microcontrolador | 2,09 | 2 | | 4,18 | Sí | Sí

Servomotor MG996R | Comedero | 2,35 | 1 | 2,73 | 5,08 | Sí | Sí
Panel solar 6V 210mA (pack) | Alimentación del dispositivo | 5,25 | 1 | 3,04 | 8,29 | Sin determinar | Sin determinar
Kit arduino | Microcontrolador | 17,43 | 1 | 0 | 17,43 | Sí | Sí
Pila recargable Samsung 18650 2600mAh | Alimentación del dispositivo | 7,99 | 1 | 0 | 7,99 | Sí | Sí
Level shifter 4 canales 3,3V a 5V (set de 10) | Radio | 1,37/set | 1 | 1,53 | 2,9 | Sí | Sí
Conectores XT30 (set de 10) | Alimentación del dispositivo/PCB | 2,25/set | 1 | 0 | 2,25 | Sí | Sí
Conectores JST (set de 20) | PCB | 1,70/set | 1 | 0,79 | 2,49 | Sí | Sí
Adaptador jack a cable (set de 5) | Alimentación del dispositivo | 1,23/set | 1 | 0 | 1,23 | Sí | Sí
Extensor SMA (15 cms) | Radio | 0,6 | 2 | 1,52 | 2,73 | Sí | Sí

Surtido resistencias | Prototipo | 1,38/set | 1 | | 1,38 | Sí | Sí
Relé 2 vías | Bebedero | 1,06 | 1 | | 1,06 | No | No
Surtido diodos | Prototipo | 1,27/set | 1 | | 1,27 | Sí | Sí
Kit conectores XH2P | PCB | 2,57/set | 1 | | 2,57 | Sí | Sí
Alimentador protoboard | Alimentación del dispositivo | 0,73 | 2 | | 1,46 | Sí | No

Step-up converter 3,3V a 5V | Alimentación del dispositivo | 0,55 | 2 | | 1,1 | Sin determinar | Sin determinar
Level shifter 8 canales 3,3 a 5V | Radio | 0,38 | 2 | | 0,76 | Sí | No
Holder batería 18650 | Alimentación del dispositivo | 0,5 | 1 | | 0,5 | Sí | Sin determinar
Conversor de 3,3 a 5V | Radio | 0,35 | 2 | | 0,7 | Sin determinar | Sin determinar
Módulo TP4056 con regulador | Alimentación del dispositivo | 0,42 | 2 | | 0,84 | Sin determinar | Sin determinar

Transistor PN2222A (set 20) | Bebedero | 1,49 | 1 | 0 | 1,49 | Sí | Sí
Relé 5V (SDR-05VDC-SL-C) | Bebedero | 3,08 | 1 | 0 | 3,08 | Sí | Sí
Transformador 220VAC a 9VDC (jack) | Alimentación del dispositivo | 3,9 | 2 | 0 | 7,8 | Sí | Sin determinar
Tubo PVC | Comedero | 2,40/m | 0,5m | NA | 1,2 | Sí | Sí
Codo 67 grados PVC | Comedero | 0,87 | 1 | NA | 0,87 | Sí | Sí
Codo 45 grados PVC | Comedero | 0,22 | 1 | NA | 0,22 | Sí | Sí
Injerto simple 87 grados PVC | Comedero | 0,57 | 1 | NA | 0,57 | Sí | Sí
Tapón ciego PVC | Comedero | 0,53 | 1 | NA | 0,53 | Sí | Sí

BMS 1S | Alimentación del dispositivo | 0,43 | 1 | 1,06 | 1,49 | Sin determinar | Sin determinar
Kit de protección batería 18650 | Alimentación del dispositivo | 3,39 | 1 | 1,48 | 4,87 | Sin determinar | Sin determinar
Transceptor LoRa E22-900T22D | Radio | 6,91 | 2 | 0 | 13,82 | Sin determinar | Sin determinar
Screw terminals (pack de 20) | Alimentación del dispositivo | 1,18 | 1 | 0,24 | 1,42 | Sin determinar | Sin determinar
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

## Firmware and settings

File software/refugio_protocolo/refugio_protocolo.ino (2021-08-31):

#include <SoftwareSerial.h>
#include "EBYTE.h"
#include <avr/io.h>
#include <Servo.h>

// v1.1a PCB
#define PUMP 7
#define LEVEL_SW1 8  // nivel superior
#define LEVEL_SW2 10 // nivel inferior
#define SERVO 9
#define PIN_RX 2
#define PIN_TX 3
#define PIN_M0 4
#define PIN_M1 5
#define PIN_AX 6

#define LORA_CHANNEL 5

#define REFILL_TIME 5000  // rellenarBebedero: 5000 ms == 5s para rellenar bebedero (default)

#define SPEED_SERVO 1500  // default: 1500. Lower value, it goes faster

#define NUM_CICLO 4       // rellenarComedero, mantener movimiento giratorio en un ciclo de rellenado

#define TOTAL_REFILL 20   // rellenarComedero, total de recargas de pienso desde reserva hasta llegar al 80% de vaciado (20% no lo contamos por seguridad)

#define BAUDRATE 115200

int num_refill = 0;       // contador de veces que se ha rellenado el comedero desde la reserva, si es igual a TOTAL_REFILL entonces dejamos de rellenar
Servo servo1;

SoftwareSerial ESerial(PIN_RX, PIN_TX); // "falso" serial para comunicarnos con el E32 (creado en SW)
EBYTE Transceiver(&ESerial, PIN_M0, PIN_M1, PIN_AX);

struct ebyte_struct {
  unsigned long count;
  char msg[64];
};
ebyte_struct ebyte_msg;

unsigned long Last;

void setup() {
  Serial.begin(BAUDRATE);
  Serial.println("Serial initialized");
  delay(300);

  // start the transceiver serial port--i have yet to get a different
  // baud rate to work--data sheet says to keep on 9600
  ESerial.begin(9600);

  // init ebyte
  Serial.println("Init transceiver");
  // this init will set the pinModes for you
  Transceiver.init();

  // all these calls are optional but shown to give examples of what you can do

  //Serial.println(Transceiver.GetAirDataRate());
  //Serial.println(Transceiver.GetChannel());

  Transceiver.SetMode(MODE_NORMAL);
  //Transceiver.SetMode(MODE_WAKEUP);

  Transceiver.SetUARTBaudRate(UDR_9600);
  Transceiver.SetAirDataRate(ADR_2400);
  Transceiver.SetAddressH(1);
  Transceiver.SetAddressL(0);

  Transceiver.SetChannel(LORA_CHANNEL);
  Transceiver.SetTransmitPower(OPT_TP21); //change transceiver tx-rx power 
  Transceiver.SetPullupMode(0);
  Transceiver.SetFECMode(1);  

  // save the parameters to the unit,
  //Transceiver.SaveParameters(PERMANENT);
  Transceiver.SaveParameters(TEMPORARY);

  // you can print all parameters and is good for debugging
  // if your units will not communicate, print the parameters
  // for both sender and receiver and make sure air rates, channel
  // and address is the same
  Transceiver.PrintParameters();

  ebyte_msg.count = 0;

  // inicializar sensores
  Serial.println("");
  pinMode(LEVEL_SW1, INPUT);
  pinMode(LEVEL_SW2, INPUT);
  pinMode(PUMP, OUTPUT);

  servo1.attach(SERVO);

  Serial.println("Ready...");
  delay(500);
}

void loop() {
  
  // if the transceiver serial is available, proces incoming data
  // you can also use Transceiver.available()

  if (ESerial.available()) {

    // i highly suggest you send data using structures and not
    // a parsed data--i've always had a hard time getting reliable data using
    // a parsing method

    Transceiver.GetStruct(&ebyte_msg, sizeof(ebyte_msg));

    // dump out what was just received
    Serial.print("ID: "); Serial.println(ebyte_msg.count);
    Serial.print("Msg: "); Serial.println(ebyte_msg.msg);
    //Serial.println("***");
    // if you got data, update the checker
    Last = millis();

    //ejecutar comandos segun llegue orden por radio

    executeCommand(ebyte_msg.msg);
   
  }
  else {
    // if the time checker is over some prescribed amount
    // let the user know there is no incoming data
    if ((millis() - Last) > 1000) {
      //Serial.println("Searching: ");
      Last = millis();
    }

  }
}

void executeCommand(String data) {
  String static msg;

  if (data.equals("status")) {
    
    
    int waterLevel = checkWaterLevel();

    int feederLevel = TOTAL_REFILL - num_refill;

    String status;

    if (waterLevel > 25 && feederLevel > 5){
      status = "ok";
    } else if (waterLevel <= 25 || feederLevel <= 5){
      status = "ko";   
    } else {
      status = "unknown";
    }

    msg = "ack;status;" + status;

    sendMessage(msg);
  }

  if (data.equals("ping")) {
    msg = "ack;pong";

    sendMessage(msg);
  }

  if (data.equals("reset_comedero")) {
    num_refill = 0;
    
    msg = "ack;reset_comedero";

    sendMessage(msg);
  }
  
  if (data.equals("rellenar_comedero")) {
    String feeder = rellenarComedero();

    msg = "ack;feeder_refill;" + feeder + ";num_refill;" + num_refill;

    sendMessage(msg);
    
  }

  if (data.equals("rellenar_bebedero")) {
    String refill = rellenarBebedero();

    msg = "ack;water_refill;" + refill;

    sendMessage(msg);
  }

  if (data.equals("check_levels")) {
    int waterLevel = checkWaterLevel();

    msg = "ack;water;" + String(waterLevel);

    sendMessage(msg);
  }

  if (data.equals("update_oled")) {
    Serial.println("to do");
  }

}
//Datos recibidos por serial, por eso printeo desde Serial.
void sendMessage(String data) {
  Serial.println("Sending data: " + data);

  // Send to radio
  data.toCharArray(ebyte_msg.msg, data.length()+1);
  ebyte_msg.count++; 
  
  Transceiver.SendStruct(&ebyte_msg, sizeof(ebyte_msg));
  Serial.println("[Refugio] Enviado. ID: " + String(ebyte_msg.count));
  //Serial.println("***");
  delay(1000);
}

int checkWaterLevel() {
  boolean sw1 = digitalRead(LEVEL_SW1);
  boolean sw2 = digitalRead(LEVEL_SW2);

  if (sw1) {
    return 100; // 100%
  } else if (sw2) {
    return 50; // 50%
  } else {
    return 25; // < 25%
  }
}

String rellenarBebedero() {
  int waterLevel = checkWaterLevel();

  if (waterLevel > 25) {
    //accionar relé para activar bomba
    Serial.println("Rellenando bebedero...");

    digitalWrite(PUMP, HIGH);
    delay(REFILL_TIME);
    digitalWrite(PUMP, LOW);

    //delay(500);

    Serial.println("Bebedero lleno");

    return "ok";
  } else {
    return "ko";
  }

}

String rellenarComedero(){

  if (num_refill >= 0 && num_refill <= TOTAL_REFILL){
    
    Serial.println("Rellenando comedero...");
    Serial.println("Contador de rellenado: " + String(num_refill));
    Serial.println("Ciclos restantes de rellenado: " + String((TOTAL_REFILL-num_refill)));
    
    for (int i = 0; i <= NUM_CICLO; i++) {    //ajustar en defines NUM_CICLO si queremos un ciclo de rellenado más largo o más corto
      //Serial.println(i);
      servo1.write(0);
      delay(SPEED_SERVO);
      servo1.write(105);
      delay(SPEED_SERVO);
    }

    // Posicion estatica
    servo1.write(90);
    delay(SPEED_SERVO);   // ajustar en define
    
    num_refill++;
    Serial.println("Ciclo " + String(num_refill) + "/20 de rellenado finalizado.");
    
    return("ok");
  } else{
    return("ko");
  }

}

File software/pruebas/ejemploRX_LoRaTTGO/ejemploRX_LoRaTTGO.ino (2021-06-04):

/* Example from Sandeep Mistry 
 * With mods from AliExpress/LilyGo docs
 * For TTGo ESP32 LoRa-OLED board
 * http://www.lilygo.cn/down_view.aspx?TypeId=11&Id=78&Fid=t14:11:14
 * Based on SX1276 LoRa Radio
 * http://www.semtech.com/apps/product.php?pn=SX1276
 * RMB 29Nov2017
 */

#include <SPI.h>
#include <LoRa.h>       // https://github.com/sandeepmistry/arduino-LoRa
#include <U8g2lib.h>   // https://github.com/olikraus/U8g2_Arduino
// #include <U8x8lib.h>

#define OFF 0   // For LED
#define ON 1

// SPI LoRa Radio
#define LORA_SCK 5        // GPIO5 - SX1276 SCK
#define LORA_MISO 19     // GPIO19 - SX1276 MISO
#define LORA_MOSI 27    // GPIO27 - SX1276 MOSI
#define LORA_CS 18     // GPIO18 - SX1276 CS
#define LORA_RST 14   // GPIO14 - SX1276 RST
#define LORA_IRQ 26  // GPIO26 - SX1276 IRQ (interrupt request)

// I2C OLED Display works with SSD1306 driver
#define OLED_SDA 4
#define OLED_SCL 15
#define OLED_RST 16

/* Pick One. Hardware I2C does NOT work! This article helped: https://robotzero.one/heltec-wifi-kit-32/ 
* TTGo boards similar to Heltec boards, LED_BUILTIN = 2 instead of pin 25
* Some OLED displays don't handle ACK correctly so SW I2C works better. Thank you Olikraus!
* TTGo OLED has pin 16 reset unlike other OLED displays
*/

// UNCOMMENT one of the constructor lines below
//U8X8_SSD1306_128X64_NONAME_SW_I2C Display(/* clock=*/ OLED_SCL, /* data=*/ OLED_SDA, /* reset=*/ OLED_RST); // Unbuffered, basic graphics, software I2C
//U8G2_SSD1306_128X64_NONAME_1_SW_I2C Display(U8G2_R0, /* clock=*/ OLED_SCL, /* data=*/ OLED_SDA, /* reset=*/ OLED_RST); // Page buffer, SW I2C
U8G2_SSD1306_128X64_NONAME_F_SW_I2C Display(U8G2_R0, /* clock=*/ OLED_SCL, /* data=*/ OLED_SDA, /* reset=*/ OLED_RST); // Full framebuffer, SW I2C

const int blueLED = LED_BUILTIN; 

String rssi = "";
String packet = "";

void setup() {
  Serial.begin(115200);
  while (!Serial);

  Serial.println("LoRa Receiver");

  Display.begin();
  Display.enableUTF8Print();    // enable UTF8 support for the Arduino print() function
  Display.setFont(u8g2_font_ncenB10_tr);

  // Very important for SPI pin configuration!
  SPI.begin(LORA_SCK, LORA_MISO, LORA_MOSI, LORA_CS); 
  
  // Very important for LoRa Radio pin configuration! 
  LoRa.setPins(LORA_CS, LORA_RST, LORA_IRQ);         

  pinMode(blueLED, OUTPUT); // For LED feedback
  
  if (!LoRa.begin(868E6)) {
    Serial.println("Starting LoRa failed!");
    while (1);  //como no queremos que siga ejecutando código si la inicialización ha fallado, escribimos esto, de manera que entramos en un bucle infinito (hasta que no se corte la alimentación o se reinicie estará sin hacer nada)
  }
  
  // The larger the spreading factor the greater the range but slower data rate
  // Send and receive radios need to be set the same
  LoRa.setSpreadingFactor(12);  // ranges from 6-12, default 7 see API docs
}

void loop() {
  // try to parse packet
  int packetSize = LoRa.parsePacket(); //analiza paquete
  if (packetSize) {                   //si hay paquete, es decir, packetSize es distinto de 0, entra 
    // received a packet
    
    Serial.print("Received packet '");

    digitalWrite(blueLED, ON);  // Turn blue LED on

    // read packet
    packet = "";                   // Clear packet
    while (LoRa.available()) {
      packet += (char)LoRa.read(); // Assemble new packet
    }
    rssi = LoRa.packetRssi();

    // Display Info
    Display.clearBuffer();  //todo esto es para terminar enviándole a la pantalla lo que queremos que muestre (no trabajamos directamente sobre la pantalla)
    Display.setCursor(0,12); Display.print("LoRa Receiver");
    Display.setCursor(0,26); Display.print("Received packet:");
    Display.setCursor(0,42); Display.print("    '" + packet + "'");
    Display.setCursor(0,58); Display.print("RSSI " + rssi);
    Display.sendBuffer();

    digitalWrite(blueLED, OFF); // Turn blue LED off
    
    Serial.println(packet + "' with RSSI " + rssi);     
  }
}

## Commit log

2021-03-12 Uploading the sketch where I combine both, controlled water pump and servo with LowPower library
2021-04-24 Planificacion.xlsx added
    [Planificación detallada.xlsx]
2021-04-24 Presupuesto.xlsx added
    [Presupuesto final.xlsx]
2021-06-04 .ino files added
    [bebedero_test.fzz, bomba.fzz, servo_connections_v1.fzz]
2021-06-22 Memoria.tex and Arduino codes updated
2021-06-25 Memoria.tex and other files updated
    [bebedero_test.fzz, servo_connections_v2.fz]
2021-08-04 web and arduino protocolo changes
2021-08-23 Servomotor explanation updated
2021-08-26 Arduino IDE and prueba 1 updated
2021-08-27 pruebas de campo section updated
2021-09-04 Revision memoria y ordenar carpetas
    [bebedero_test.fzz, bomba.fzz, servo_connections_v1.fzz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]
2021-09-09 revision antiplagio
    [Pieza sujeción bebedero.stl, Water_Tank_Level_Sensor.fzz]
